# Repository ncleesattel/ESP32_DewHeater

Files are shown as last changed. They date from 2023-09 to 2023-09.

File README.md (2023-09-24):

# ESP32_DewHeater
Dew heater using the MyDewHeater from Robert Brown as starting point to understand circutry and software.

## Hardware Features
* Integration in Bopla Alubos case equal in size to the TeenAstro Main Unit.
* Design comprised of 3x pcbs
   * main dew heater circutry
   * connection panel top
   * sensor panel bottom
* Design uses SMDs to make use of the JLCPCB assembly service.

### Power Distribution
* Breakout DC-power jacks for
   * TeenAstro Main Unit
   * Intel NUC or Lenovo ThinkCentre
   * AstroCam
   * Filter-Rotator
### Dew Heater
* 3-Channel output that can be used for dew straps or a flat-field light.
* Use of high efficiency MOSFETs to eliminate need for heat sink.
* Integration of current and voltage sensors to calculate actual power output.
* Use of BME280 sensor to calculate dew point.
* Use of rotary pulse encoders to adjust power output.

## Software Features
* Bare knuckle software without closed-loop shenanigans.
* Read sensors and rotary pulse encoders.
* Calculate power output and dew point.
* Adjust output with enoder input only.

## BOM
What do you need for this build.
* dew_control_pcb
* dew_connector_pcb
* dew_sensor_pcb
* OLED 2.42" from DIYMORE configured to I2C or similar
* ESP32 30-pin MCU
* Bopla Alubos ABPH-1300-0150 bottom half
* 3D print for top cover which also fits display
* 3D print of side cover connector
* 3D print of side cover sensor
* 2x Mentor aluminum knobs 521.611
* 3x RCA connector Cliff FC68375
* 8x DC-jack Cliff FC681445 (5.5mm x 2.1mm type)
* 6x JST VH VHR-2N connectors for 3 cables
* 3x JST VH B2P-VH (LF) connector to solder to pcbs
* TE Mate N Lok 350211-1 connector to solder to pcb
* Marquart Series 1800 switch (on/off)
* Ruthex M2.5 threaded inserts

## Cost estimate
| Item | Number | Cost |
|-----|-----|-----|
| dew_control_pcb | 5 | 160|
| dew_sensor_pcb | 5 | 15|
| dew_connector_pcb | 5 | 15|
| ESP32 30-in MCU | 1 | 10|
| OLED 2.42 | 1 | 20|
| BOPLA Alubos ABPH 1300-0150 | 1 | 50|
| Cliff RCA connectors | 3 | 10 |
| Cliff DC jacks | 8 | 24 |
| various other | x | 20 |

Best case 170 Eur if you can share all pcbs  
Worst case 320 Eur if you keep all pcbs and build only one

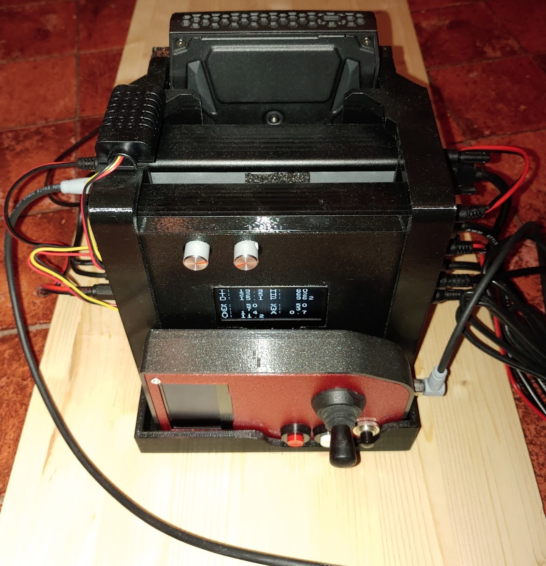
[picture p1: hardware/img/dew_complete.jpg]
running


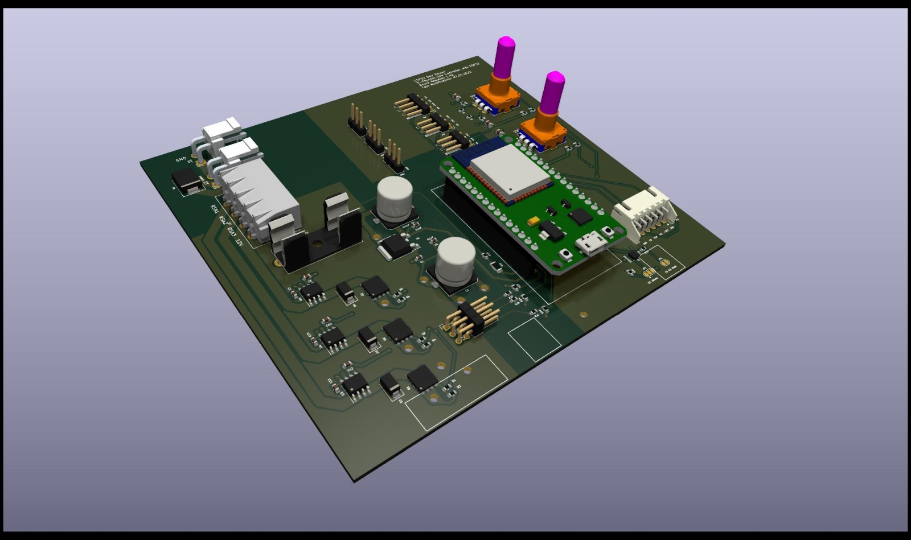
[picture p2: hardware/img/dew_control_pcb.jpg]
control_pcb


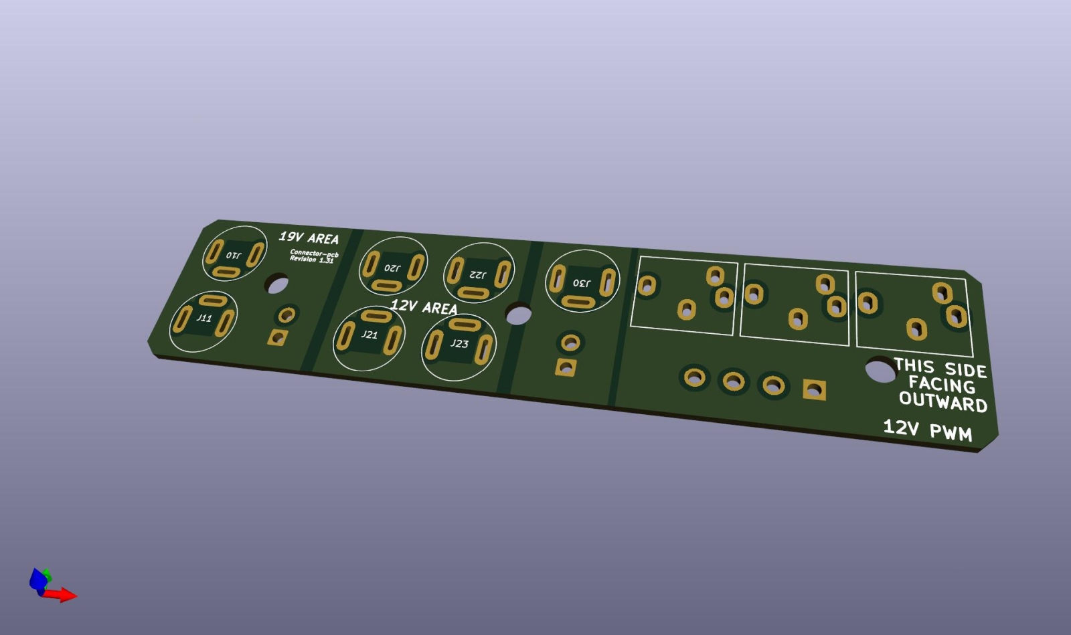
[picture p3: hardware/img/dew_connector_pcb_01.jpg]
connector_pcb


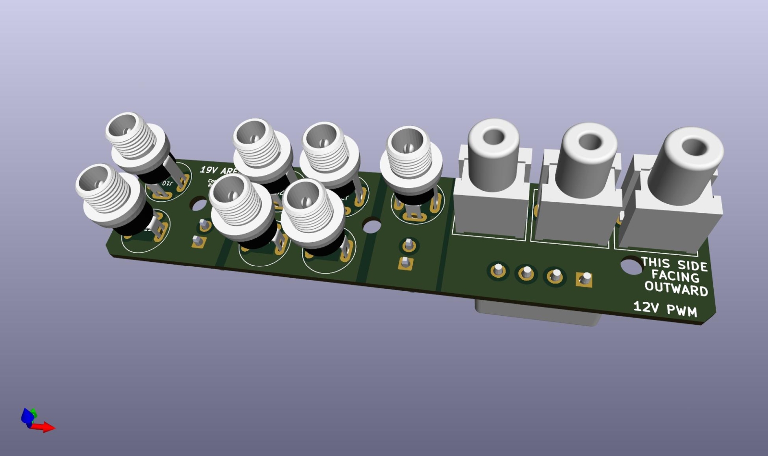
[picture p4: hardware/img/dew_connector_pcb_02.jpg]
connector_pcb


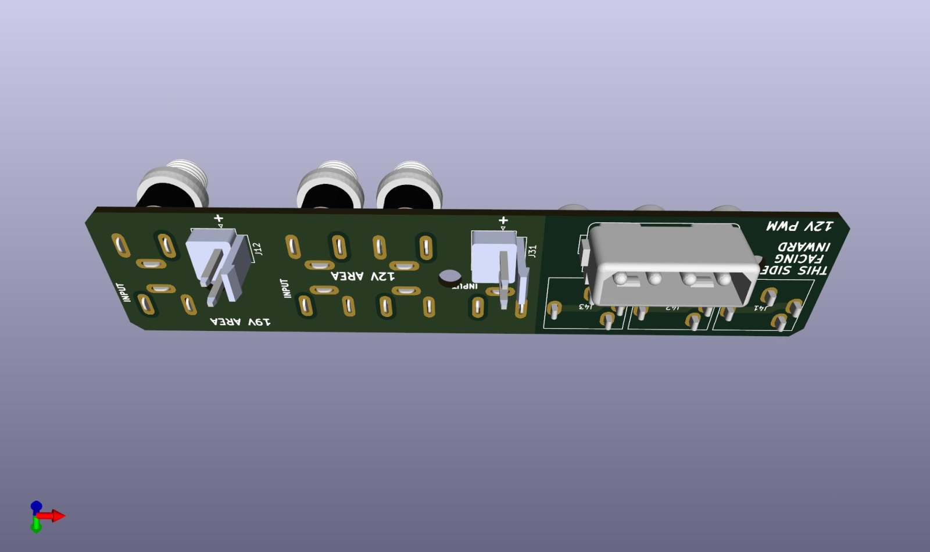
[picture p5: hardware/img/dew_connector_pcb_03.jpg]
connector_pcb


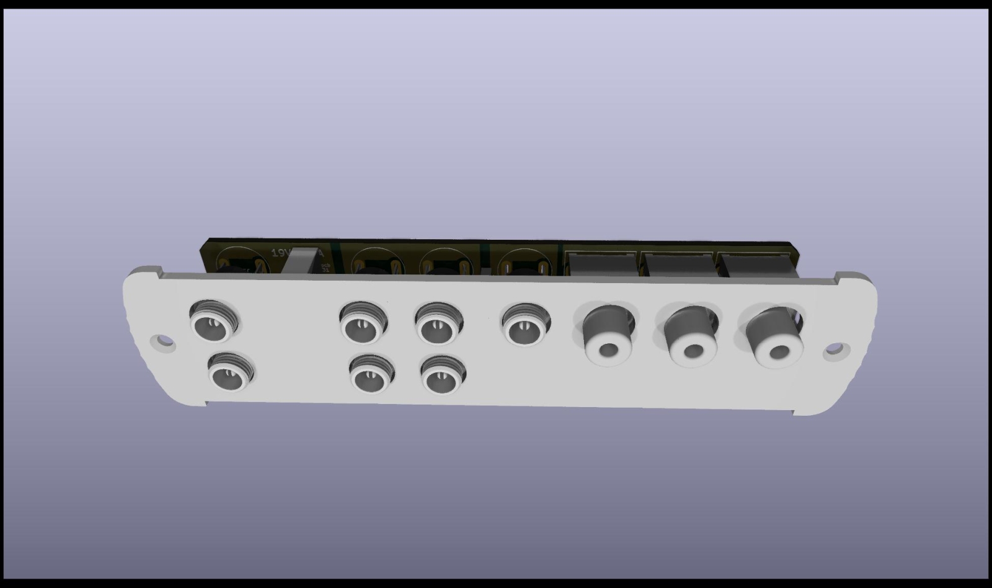
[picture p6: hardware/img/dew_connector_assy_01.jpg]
connector_assy


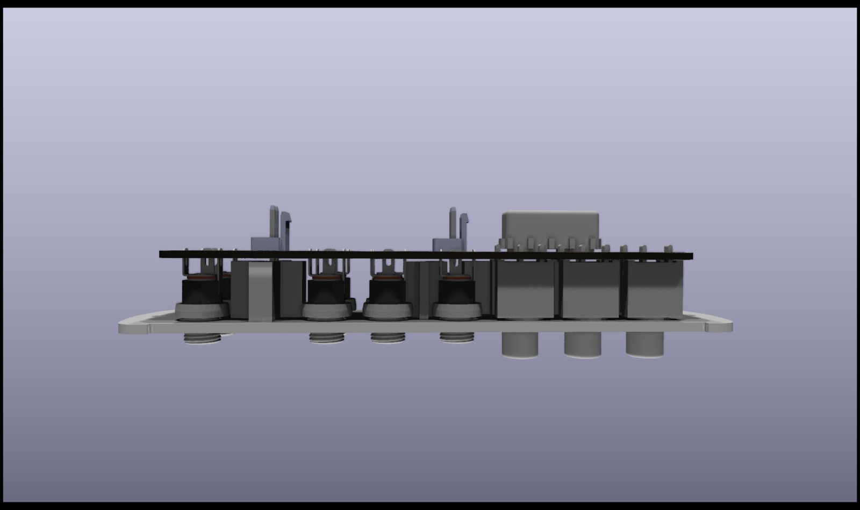
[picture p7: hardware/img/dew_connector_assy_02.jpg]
connector_assy


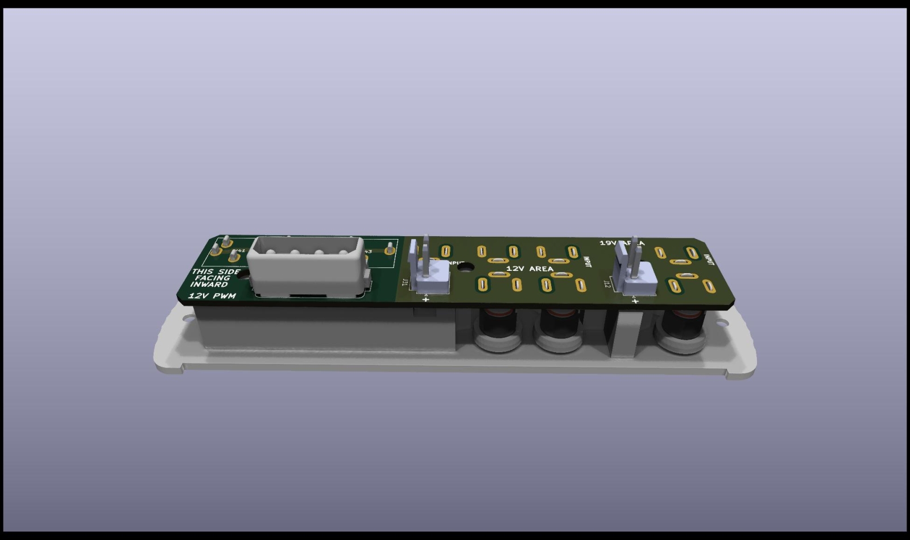
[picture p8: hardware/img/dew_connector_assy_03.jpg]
connector_assy


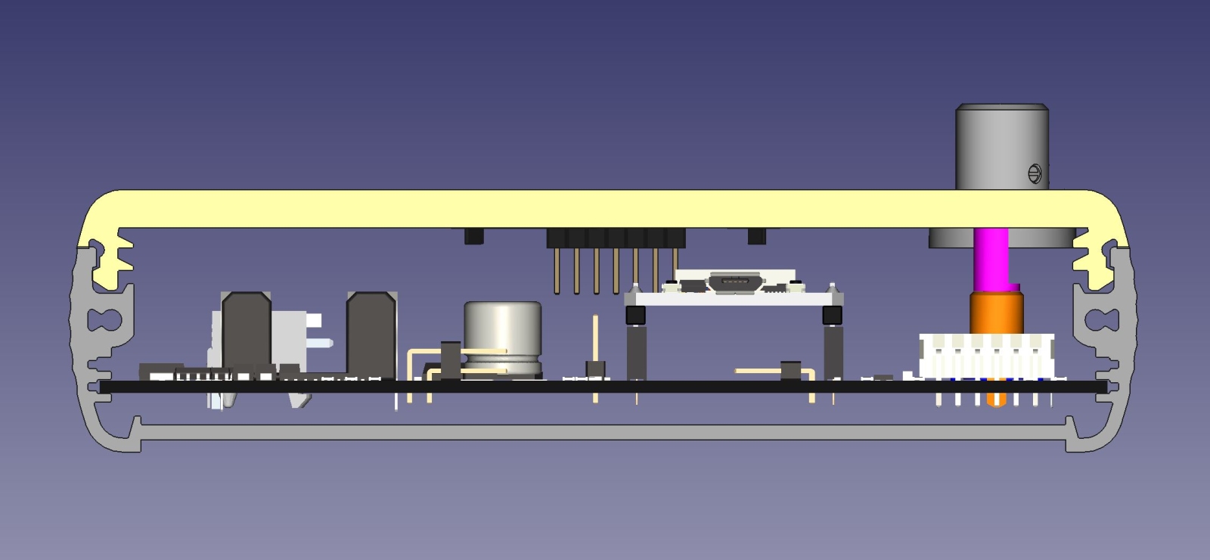
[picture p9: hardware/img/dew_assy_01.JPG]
dew_assy


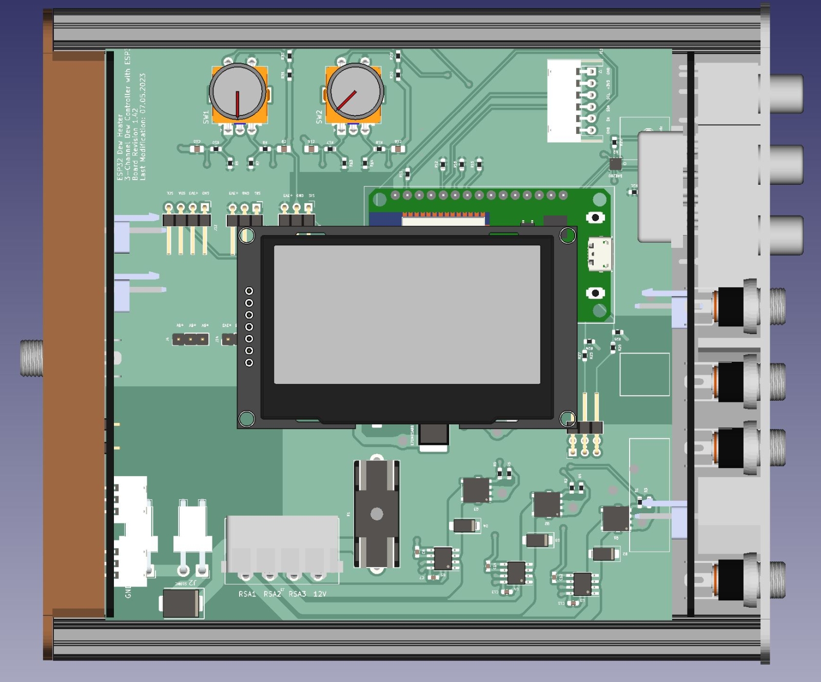
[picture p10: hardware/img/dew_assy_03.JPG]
dew_assy


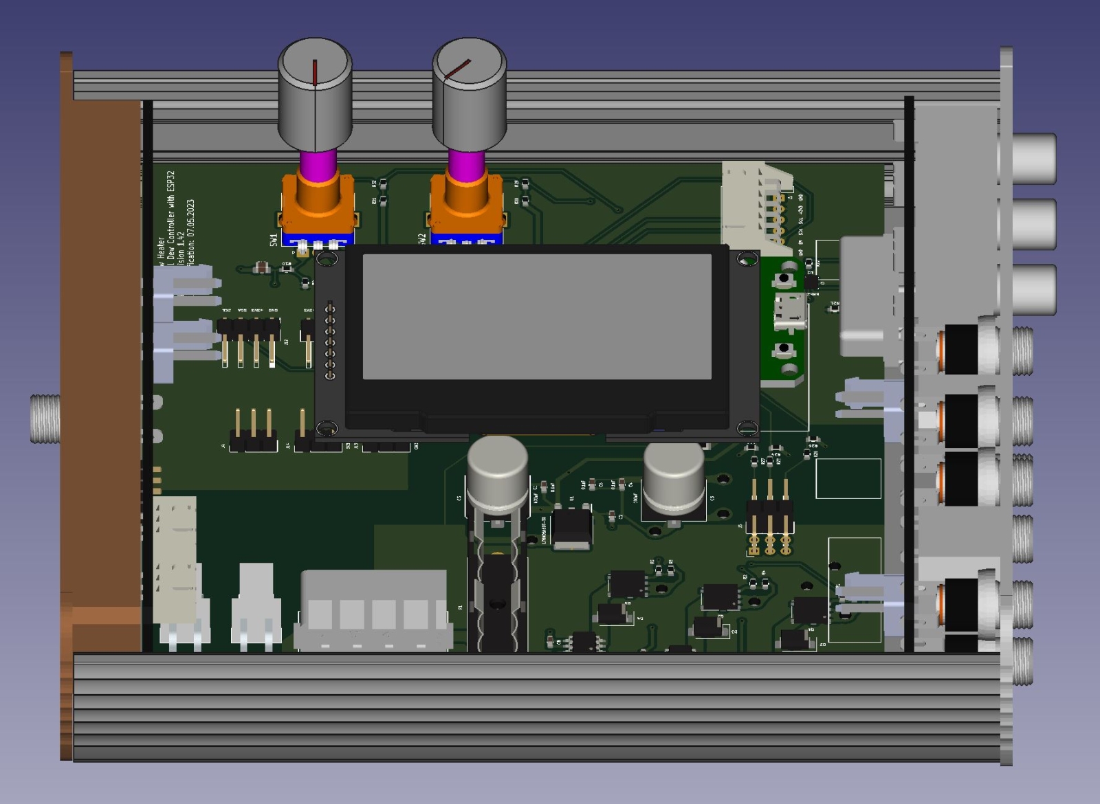
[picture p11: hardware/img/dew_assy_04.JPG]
dew_assy


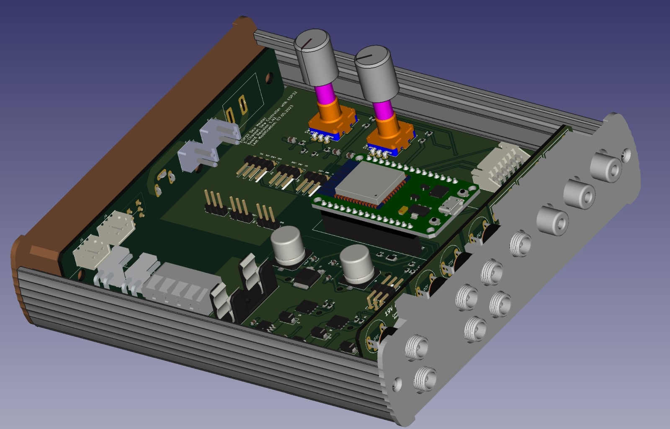
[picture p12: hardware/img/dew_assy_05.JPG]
dew_assy


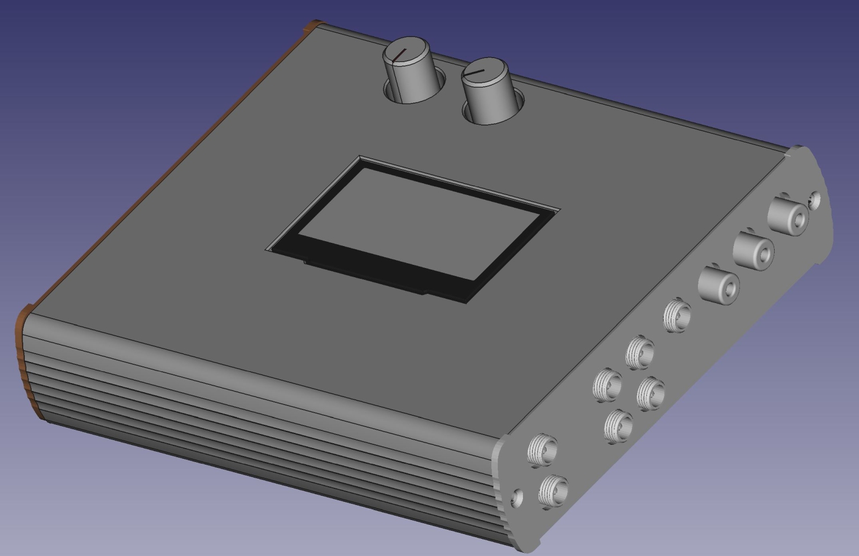
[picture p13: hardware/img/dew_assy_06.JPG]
dew_assy


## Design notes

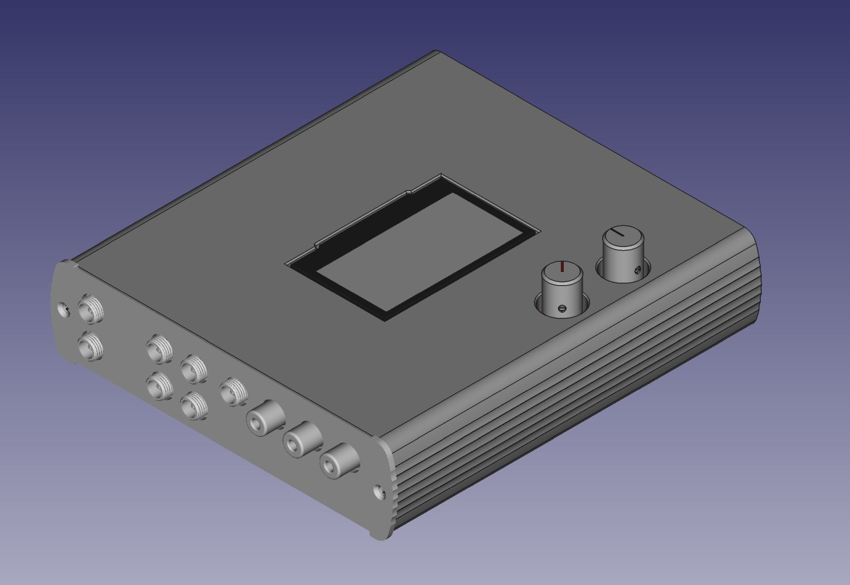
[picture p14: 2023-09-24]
hardware/img/dew_assy_02.JPG

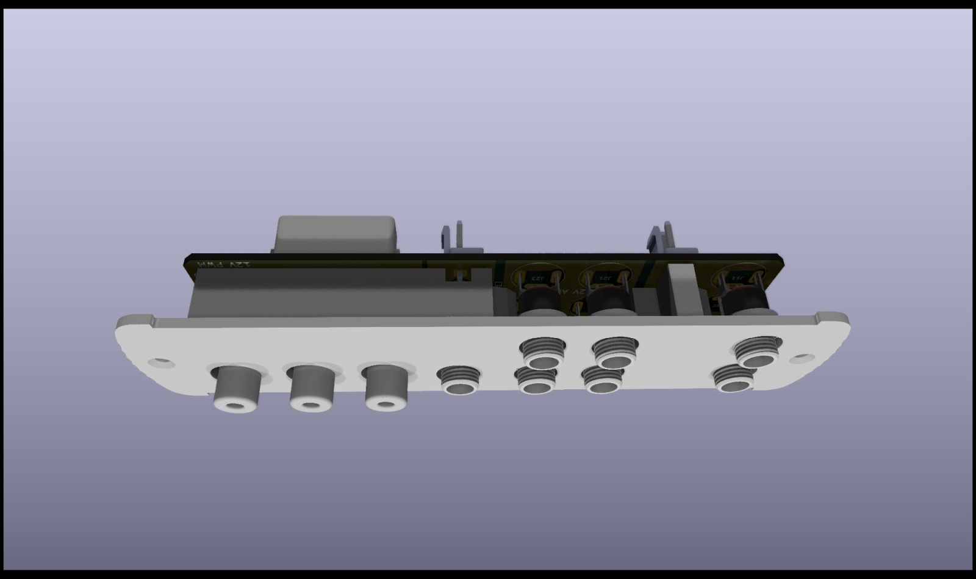
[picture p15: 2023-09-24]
hardware/img/dew_connector_assy_04.jpg

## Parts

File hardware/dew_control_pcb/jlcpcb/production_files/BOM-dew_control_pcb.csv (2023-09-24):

Comment | Designator | Footprint | LCSC
0.1uF | C1,C11,C13,C4,C6,C7 | C_0603_1608Metric | C14663
OLED | J11 | JST_XH_S6B-XH-A_1x06_P2.50mm_Horizontal | C157919
POWER | J1,J2 | JST_VH_S2P-VH_1x02_P3.96mm_Horizontal | C160355
0.33uF | C2 | C_0603_1608Metric | C1615
S10MC | D1 | D_SMC | C169472
NTMFS5C670NLT1G | Q1,Q2,Q3 | ONSemi_SO-8FL_488AA | C179626
Fuse | F1 | Fuseholder_Cylinder-5x20mm | C206887
150 | R1,R2,R5 | R_0603_1608Metric | C22808
15K | R23,R25,R27 | R_0603_1608Metric | C22809
4K7 | R11,R12,R15,R16,R20,R21 | R_0603_1608Metric | C23162
43k | R24,R26,R28 | R_0603_1608Metric | C23172
CURRENT EN | J5 | PinHeader_2x03_P2.54mm_Horizontal | C239334
10K | R10,R13,R14,R17,R18,R19,R29,R3,R30,R31,R32,R4,R6,R7,R8,R9 | R_0603_1608Metric | C25804
1.5K | R22 | R_1206_3216Metric | C26036
100uF | C5 | C_Elec_10x10.2 | C280414
I2C | J12 | PinHeader_1x04_P2.54mm_Horizontal | C293357
0.01uF | C10,C15,C16,C9 | C_0805_2012Metric | C376921
ACS712xLCTR-05B | U3,U4,U5 | SOIC-8_3.9x4.9mm_P1.27mm | C44471
RotaryEncoder_Switch | SW1,SW2 | RotaryEncoder_Alps_EC11E-Switch_Vertical_H20mm | C470754
RSA DEW | J3 | TE_MATE-N-LOK_1x04_P5.08mm_Horizontal | C492552
L78M05ABDT-TR | U1 | TO-252-2 | C58069
PROBE1 | J31,J32 | PinHeader_1x03_P2.54mm_Horizontal | C706866
470uF | C3 | C_Elec_10x10.2 | C72518
D_Schottky | D2,D3,D4 | D_SMA | C8678
1nF | C12,C14,C8 | C_0603_1608Metric | C8808
BME280 | U2 | Bosch_LGA-8_2.5x2.5mm_P0.65mm_ClockwisePinNumbering | C92489
I2C Adress | JP2 | SolderJumper-3_P1.3mm_Bridged12_RoundedPad1.0x1.5mm
3V3 | J14 | PinHeader_1x03_P2.54mm_Vertical
GND | J13 | PinHeader_1x03_P2.54mm_Vertical
ESP32-30pin | IC1 | ESP32-30pin
5V | J4 | PinHeader_1x03_P2.54mm_Vertical
EN I2C Mode | JP1 | SolderJumper-2_P1.3mm_Bridged_RoundedPad1.0x1.5mm

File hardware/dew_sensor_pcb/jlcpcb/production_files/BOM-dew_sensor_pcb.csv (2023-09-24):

Comment | Designator | Footprint | LCSC
Conn_01x03 | J7 | PinHeader_1x03_P2.54mm_Vertical
Conn_01x02 | J1 | JST_VH_B2P-VH-B_1x02_P3.96mm_Vertical
Conn_01x02 | J2 | JST_VH_B2P-VH-B_1x02_P3.96mm_Vertical
SW_SPST | SW1 | Marquart
Conn_01x03 | J4 | JST_XH_B3B-XH-A_1x03_P2.50mm_Vertical
Conn_01x03 | J6 | JST_XH_B3B-XH-A_1x03_P2.50mm_Vertical
Conn_01x03 | J5 | PinHeader_1x03_P2.54mm_Vertical
Barrel_Jack_MountingPin | J8 | BarrelJack_Vertical

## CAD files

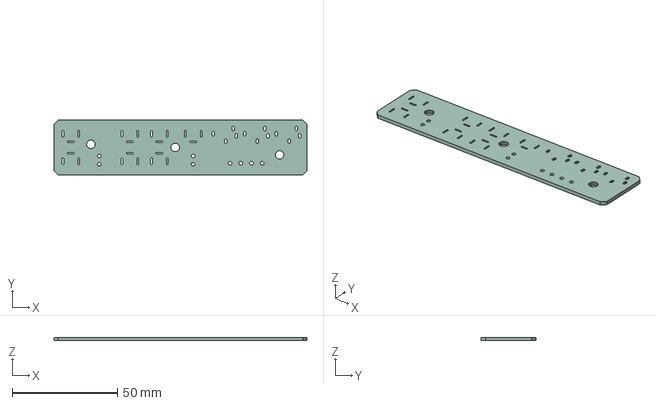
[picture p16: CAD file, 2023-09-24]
hardware/dew_connector_pcb/dew_connector_pcb.step
120.0 x 26.0 x 1.58 mm

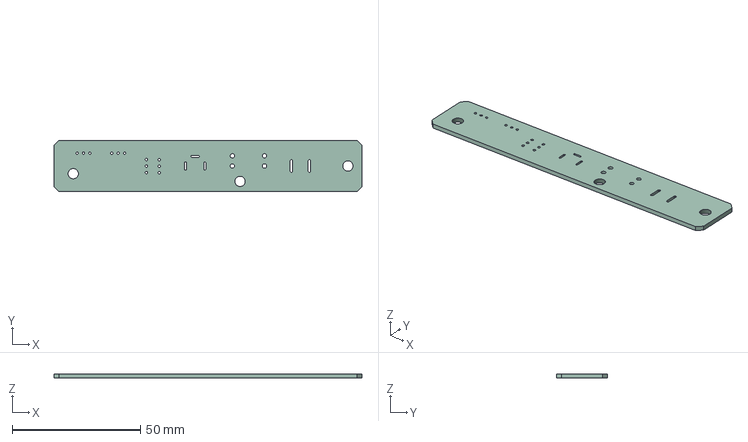
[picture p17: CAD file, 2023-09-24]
hardware/dew_sensor_pcb/dew_sensor_pcb.step
120.0 x 20.0 x 1.58 mm

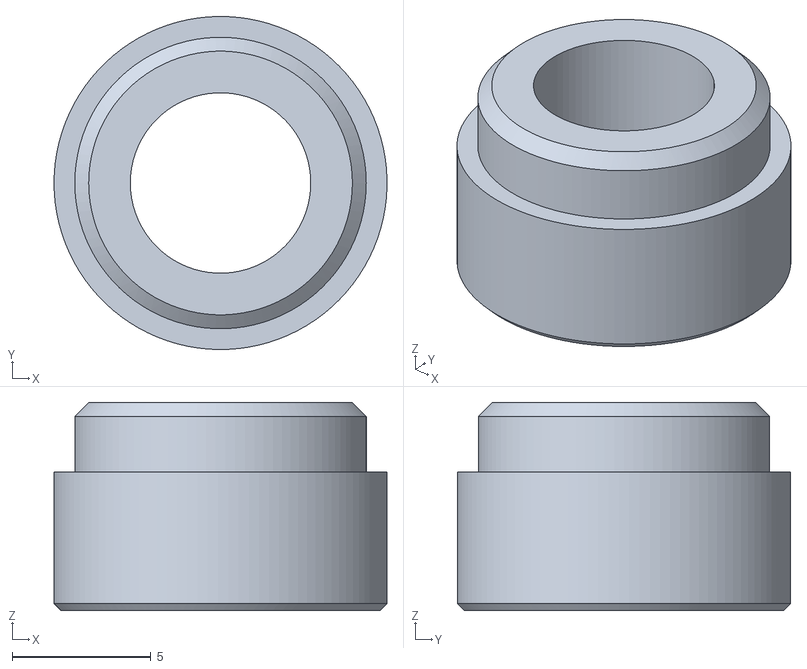
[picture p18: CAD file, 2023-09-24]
hardware/models/KNOB_SOCKET.stl
12.0 x 12.0 x 7.50

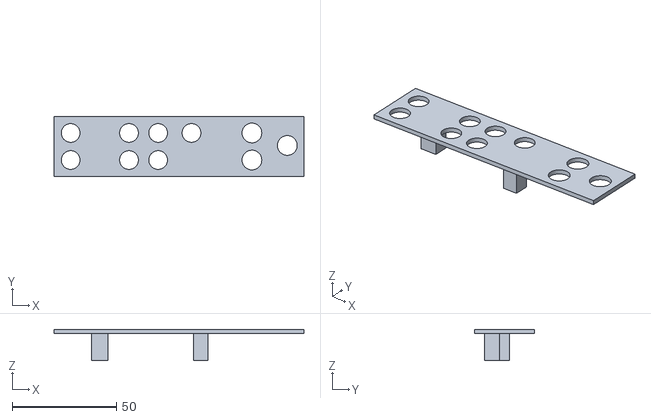
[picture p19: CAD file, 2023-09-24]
hardware/models/SOLDERING_HELP.stl
120.0 x 29.0 x 15.0

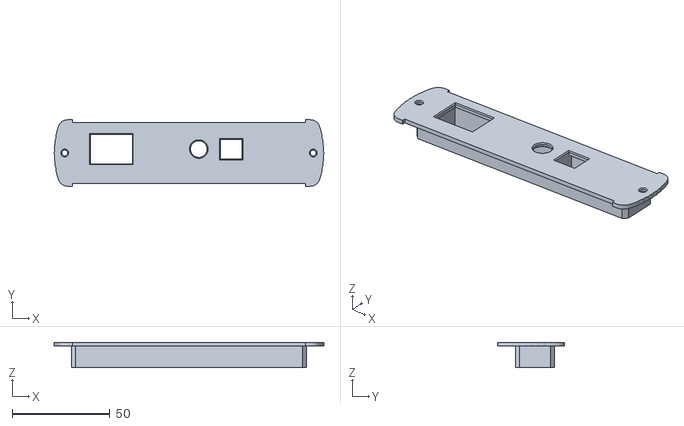
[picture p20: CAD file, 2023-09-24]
hardware/models/OUTPUT_PRINT.stl
138.0 x 34.0 x 13.0

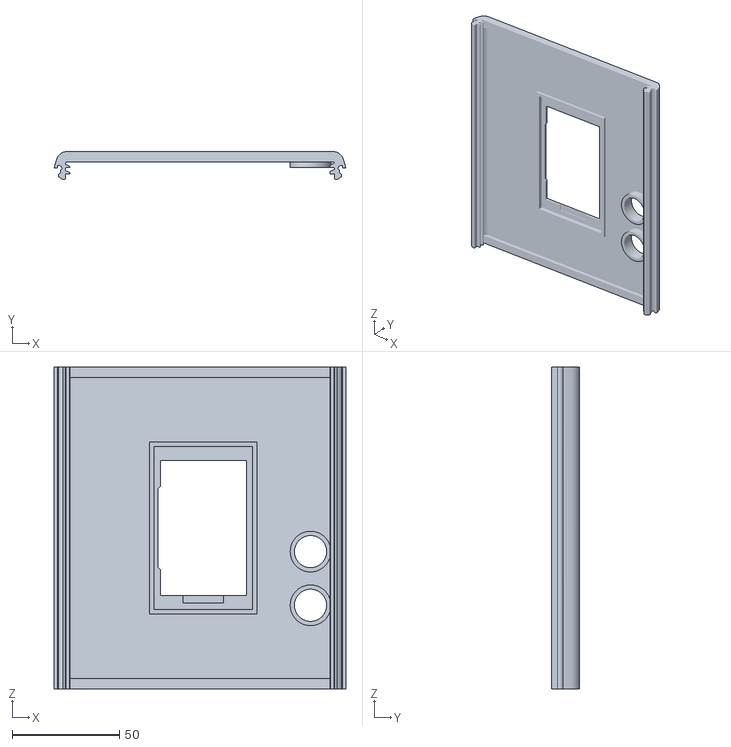
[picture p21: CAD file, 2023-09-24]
hardware/models/DISPLAY_PRINT.stl
135.8 x 13.0 x 150.0

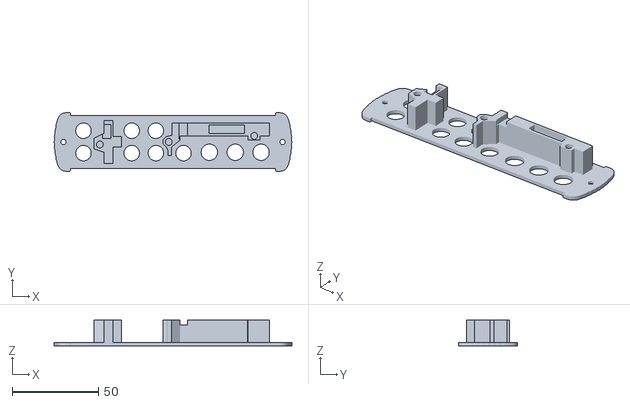
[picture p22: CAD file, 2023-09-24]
hardware/models/CONNECTOR_PRINT.stl
138.0 x 34.0 x 15.0

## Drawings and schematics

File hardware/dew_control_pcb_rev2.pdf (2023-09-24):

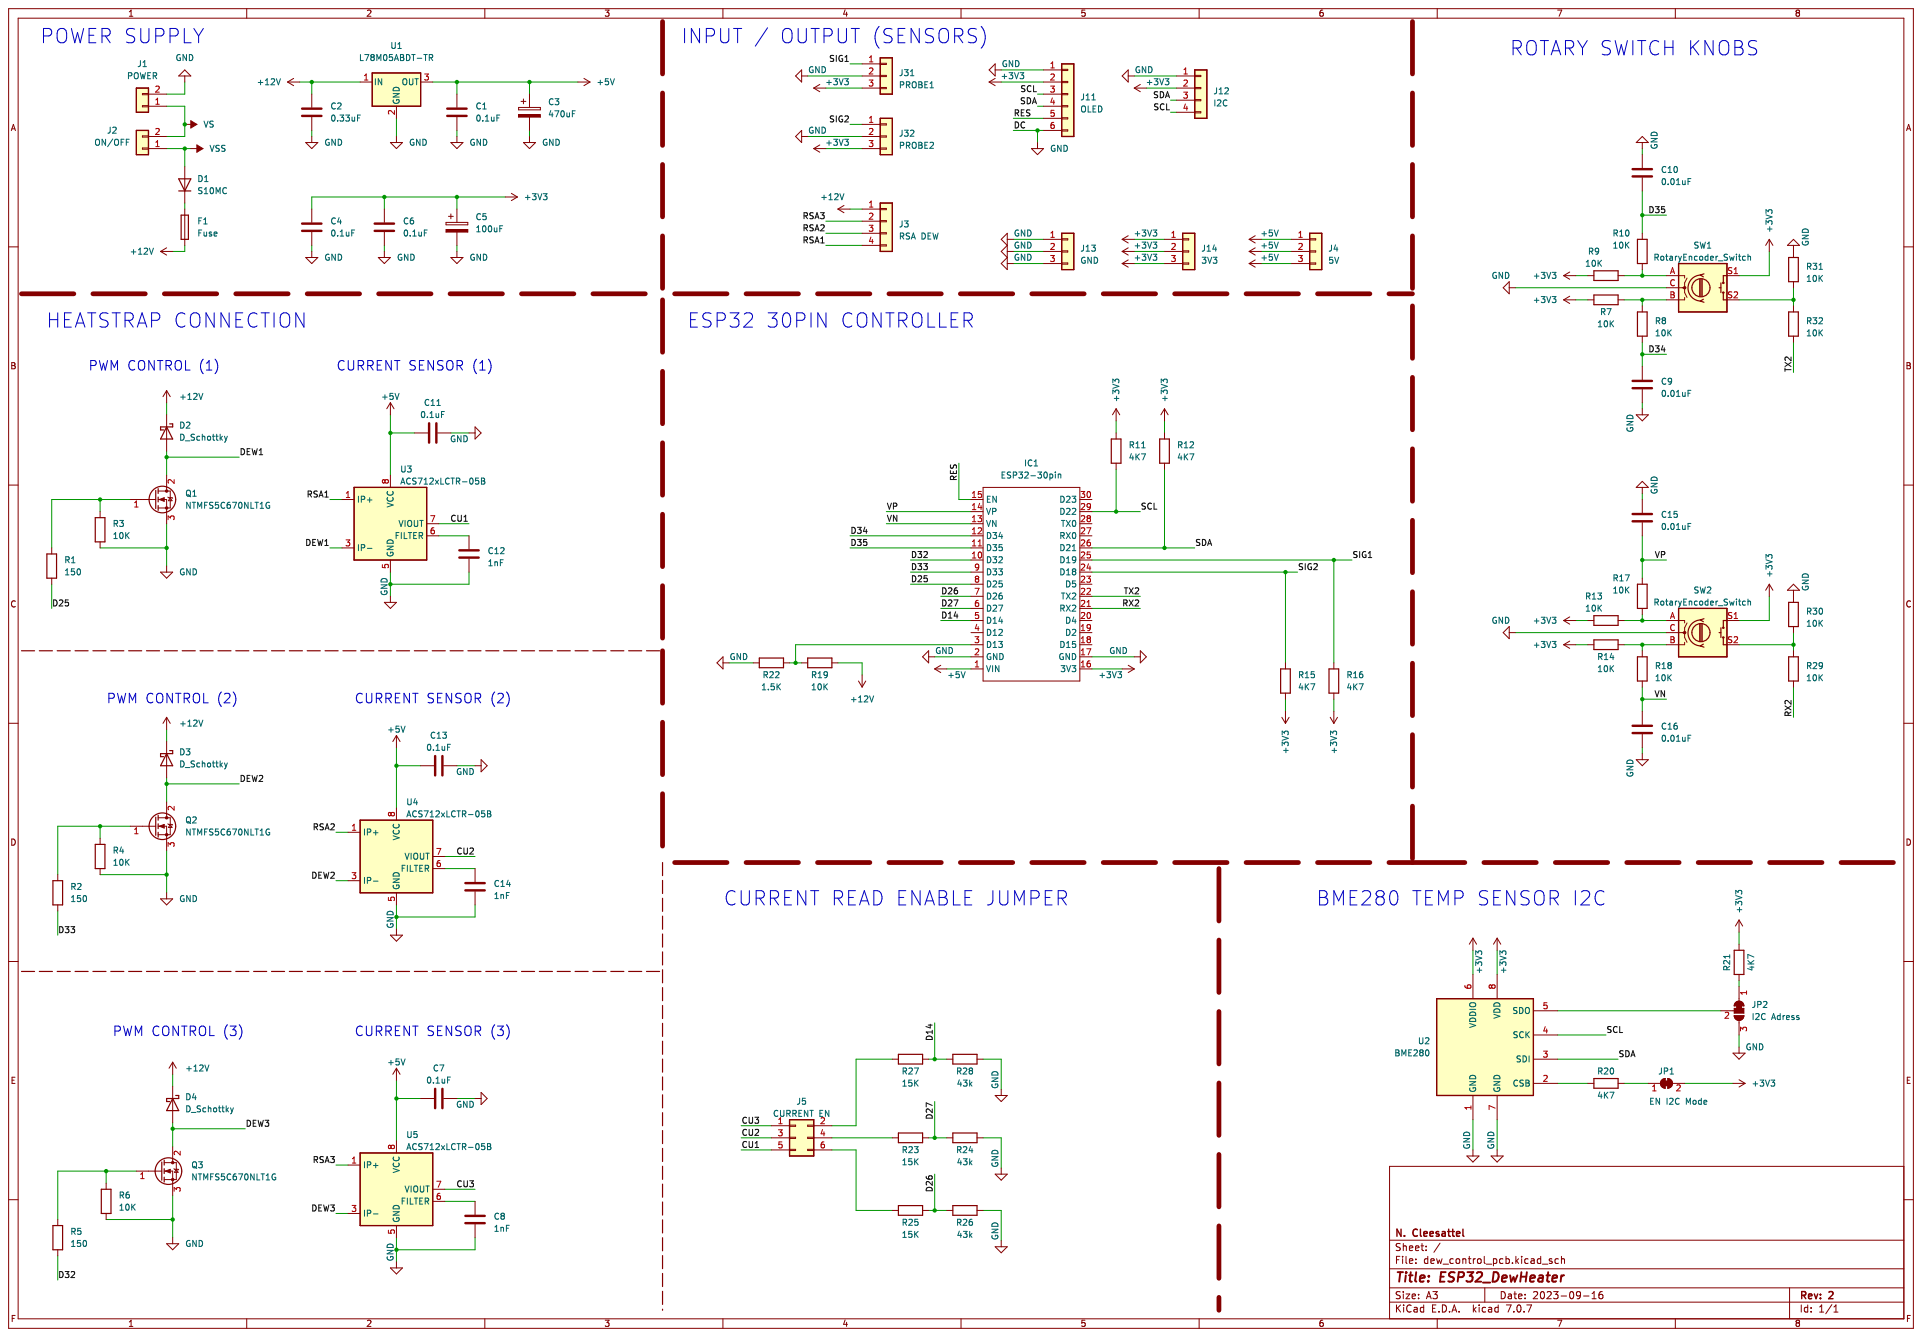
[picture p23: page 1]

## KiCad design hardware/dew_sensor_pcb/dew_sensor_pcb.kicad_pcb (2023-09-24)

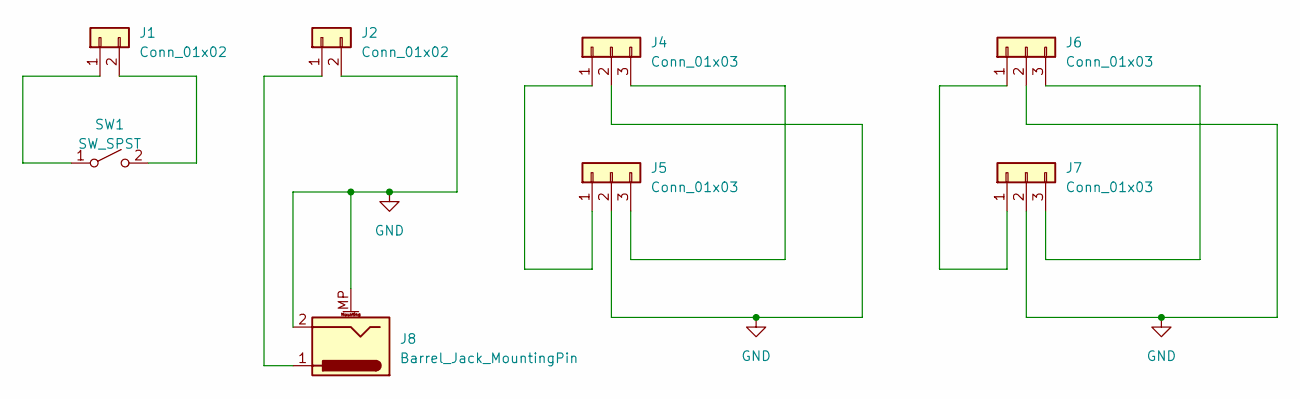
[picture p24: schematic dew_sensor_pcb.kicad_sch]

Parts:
J1, J2: Conn_01x02; JST_VH_B2P-VH-B_1x02_P3.96mm_Vertical
J4, J6: Conn_01x03; JST_XH_B3B-XH-A_1x03_P2.50mm_Vertical
J5, J7: Conn_01x03; PinHeader_1x03_P2.54mm_Vertical
J8: Barrel_Jack_MountingPin; BarrelJack_Vertical
SW1: SW_SPST; Marquart

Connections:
GND: J2.2, J4.2, J5.2, J6.2, J7.2, J8.2, J8.MP (MountPin)
unnamed: J1.1, SW1.1 (A)
unnamed: J1.2, SW1.2 (B)
unnamed: J2.1, J8.1
unnamed: J4.1, J5.1
unnamed: J4.3, J5.3
unnamed: J6.1, J7.1
unnamed: J6.3, J7.3

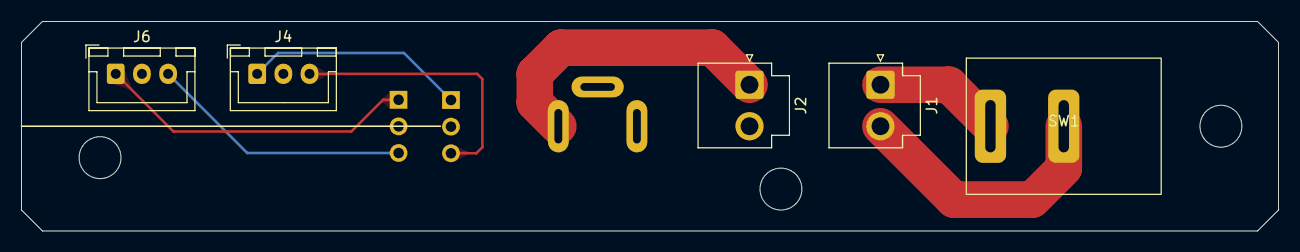
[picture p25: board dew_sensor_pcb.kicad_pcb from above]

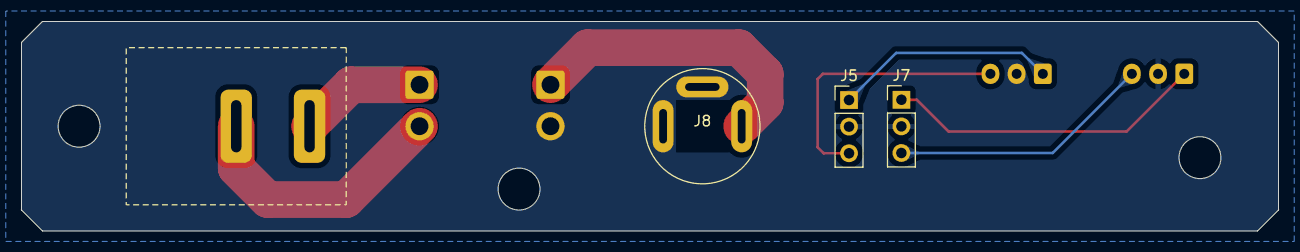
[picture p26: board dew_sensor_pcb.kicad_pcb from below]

Board: 2 copper layers, 120.0 x 20.0 mm, 8 parts (3 on the bottom side), 8 nets.

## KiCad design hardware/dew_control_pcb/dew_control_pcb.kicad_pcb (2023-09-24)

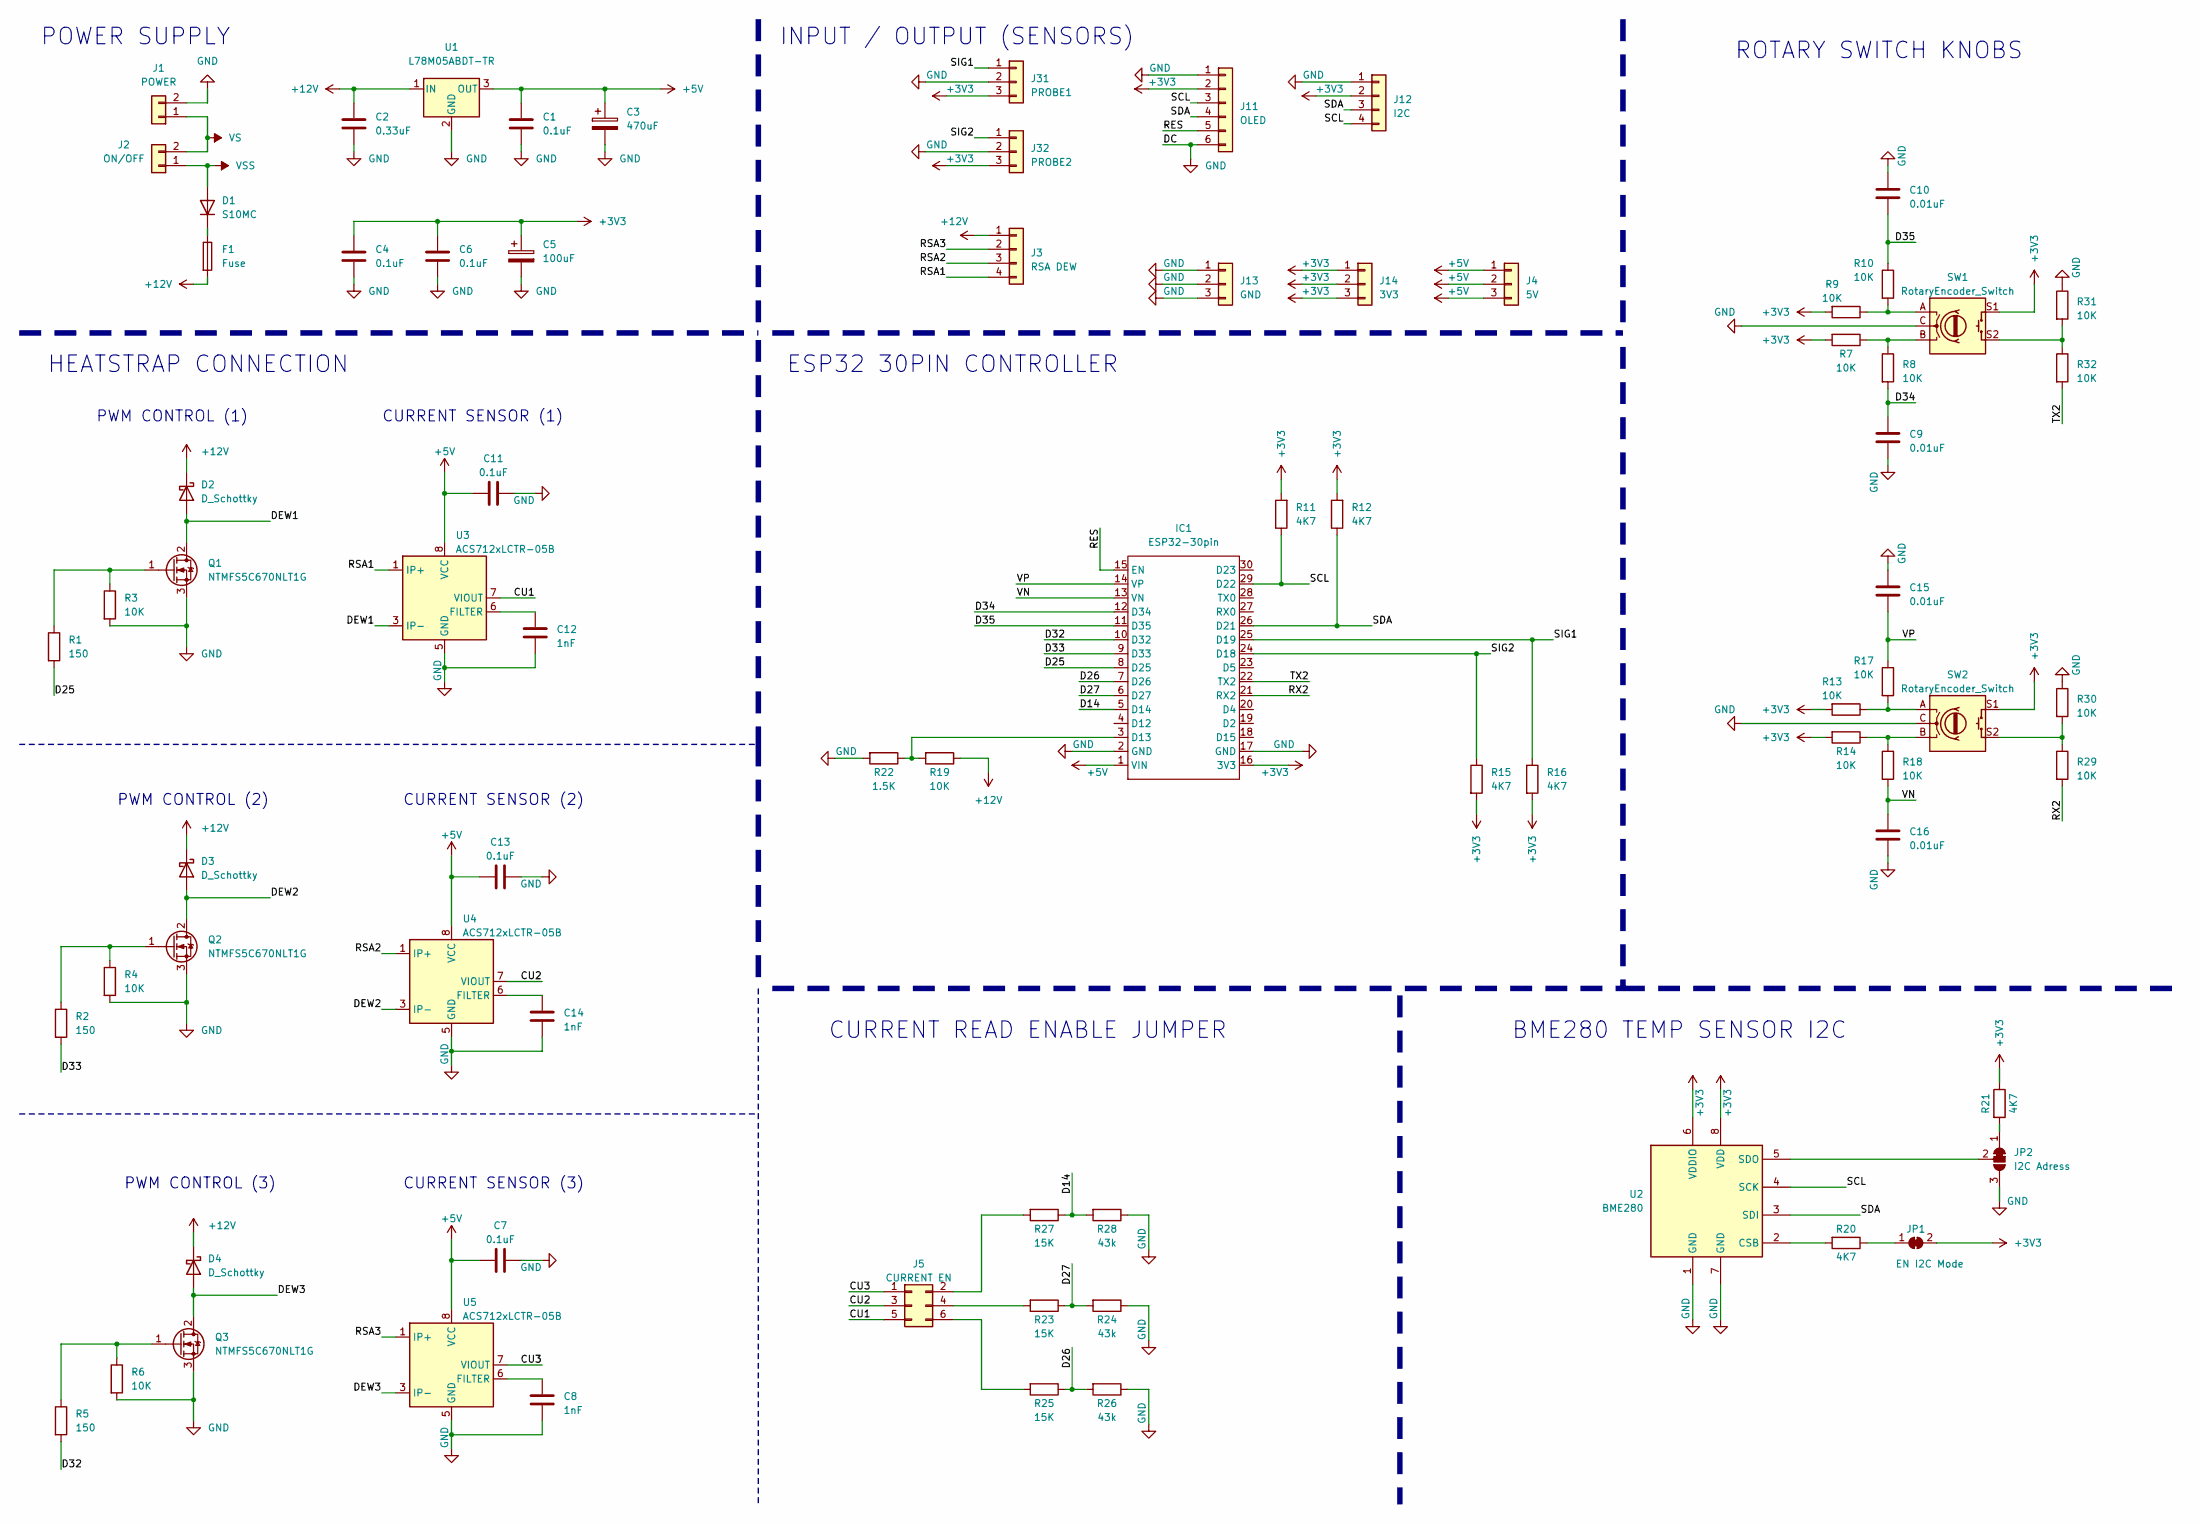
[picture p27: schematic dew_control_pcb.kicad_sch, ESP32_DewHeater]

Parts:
C1, C4, C6, C7, C11, C13: 0.1uF; C_0603_1608Metric; LCSC C14663
C2: 0.33uF; C_0603_1608Metric; LCSC C1615
C3: 470uF; C_Elec_10x10.2; LCSC C72518
C5: 100uF; C_Elec_10x10.2; LCSC C280414
C8, C12, C14: 1nF; C_0603_1608Metric; LCSC C8808
C9, C10, C15, C16: 0.01uF; C_0805_2012Metric; LCSC C376921
D1: S10MC; D_SMC; LCSC C169472
D2, D3, D4: D_Schottky; D_SMA; JLCPCB C8678
F1: Fuse; Fuseholder_Cylinder-5x20mm; LCSC C206887
IC1: ESP32-30pin
J1: POWER; JST_VH_S2P-VH_1x02_P3.96mm_Horizontal; LCSC C160355
J2: ON/OFF; JST_VH_S2P-VH_1x02_P3.96mm_Horizontal; LCSC C160355
J3: RSA DEW; TE_MATE-N-LOK_1x04_P5.08mm_Horizontal; LCSC C492552
J4: 5V; PinHeader_1x03_P2.54mm_Vertical
J5: CURRENT EN; PinHeader_2x03_P2.54mm_Horizontal; LCSC C239334
J11: OLED; JST_XH_S6B-XH-A_1x06_P2.50mm_Horizontal; LCSC C157919
J12: I2C; PinHeader_1x04_P2.54mm_Horizontal; LCSC C293357
J13: GND; PinHeader_1x03_P2.54mm_Vertical
J14: 3V3; PinHeader_1x03_P2.54mm_Vertical
J31: PROBE1; PinHeader_1x03_P2.54mm_Horizontal; LCSC C706866
J32: PROBE2; PinHeader_1x03_P2.54mm_Horizontal; LCSC C706866
JP1: EN I2C Mode; SolderJumper-2_P1.3mm_Bridged_RoundedPad1.0x1.5mm
JP2: I2C Adress; SolderJumper-3_P1.3mm_Bridged12_RoundedPad1.0x1.5mm
Q1, Q2, Q3: NTMFS5C670NLT1G; ONSemi_SO-8FL_488AA; LCSC C179626
R1, R2, R5: 150; R_0603_1608Metric; LCSC C22808
R3, R4, R6, R7, R8, R9, R10, R13, R14, R17, R18, R19, R29, R30, R31, R32: 10K; R_0603_1608Metric; LCSC C25804
R11, R12, R15, R16, R20, R21: 4K7; R_0603_1608Metric; LCSC C23162
R22: 1.5K; R_1206_3216Metric; LCSC C26036
R23, R25, R27: 15K; R_0603_1608Metric; LCSC C22809
R24, R26, R28: 43k; R_0603_1608Metric; LCSC C23172
SW1, SW2: RotaryEncoder_Switch; RotaryEncoder_Alps_EC11E-Switch_Vertical_H20mm; LCSC C470754
U1: L78M05ABDT-TR; TO-252-2; LCSC C58069
U2: BME280; Bosch_LGA-8_2.5x2.5mm_P0.65mm_ClockwisePinNumbering; LCSC C92489
U3, U4, U5: ACS712xLCTR-05B; SOIC-8_3.9x4.9mm_P1.27mm; LCSC C44471

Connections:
+3V3: C4.1, C5.1, C6.1, IC1.16 (3V3), J11.2, J12.2, J14.1, J14.2, J14.3, J31.3, J32.3, JP1.2 (B), R7.2, R9.2, R11.2, R12.2, R13.2, R14.2, R15.2, R16.2, R21.1, SW1.S1, SW2.S1, U2.6 (VDDIO), U2.8 (VDD)
+5V: C1.1, C3.1, C7.1, C11.1, C13.1, IC1.1 (VIN), J4.1, J4.2, J4.3, U1.3 (OUT), U3.8 (VCC), U4.8 (VCC), U5.8 (VCC)
+12V: C2.1, D2.1 (K), D3.1 (K), D4.1 (K), F1.2, J3.1, R19.1, U1.1 (IN)
/CU1: J5.5, U3.7 (VIOUT)
/CU2: J5.3, U4.7 (VIOUT)
/CU3: J5.1, U5.7 (VIOUT)
/D14: IC1.5 (D14), R27.1, R28.2
/D25: IC1.8 (D25), R1.2
/D26: IC1.7 (D26), R25.1, R26.2
/D27: IC1.6 (D27), R23.1, R24.2
/D32: IC1.10 (D32), R5.2
/D33: IC1.9 (D33), R2.2
/D34: C9.1, IC1.12 (D34), R8.2
/D35: C10.2, IC1.11 (D35), R10.1
/DEW1: D2.2 (A), Q1.2 (D), U3.3 (IP-), U3.4 (IP-)
/DEW2: D3.2 (A), Q2.2 (D), U4.3 (IP-), U4.4 (IP-)
/DEW3: D4.2 (A), Q3.2 (D), U5.3 (IP-), U5.4 (IP-)
/RES: IC1.15 (EN), J11.5
/RSA1: J3.4, U3.1 (IP+), U3.2 (IP+)
/RSA2: J3.3, U4.1 (IP+), U4.2 (IP+)
/RSA3: J3.2, U5.1 (IP+), U5.2 (IP+)
/RX2: IC1.21 (RX2), R29.2
/SCL: IC1.29 (D22), J11.3, J12.4, R11.1, U2.4 (SCK)
/SDA: IC1.26 (D21), J11.4, J12.3, R12.1, U2.3 (SDI)
/SIG1: IC1.25 (D19), J31.1, R16.1
/SIG2: IC1.24 (D18), J32.1, R15.1
/TX2: IC1.22 (TX2), R32.2
/VN: C16.1, IC1.13 (VN), R18.2
/VP: C15.2, IC1.14 (VP), R17.1
GND: C1.2, C2.2, C3.2, C4.2, C5.2, C6.2, C7.2, C8.1, C9.2, C10.1, C11.2, C12.1, C13.2, C14.1, C15.1, C16.2, IC1.2 (GND), IC1.17 (GND), J1.2, J11.1, J11.6, J12.1, J13.1, J13.2, J13.3, J31.2, J32.2, JP2.3 (B), Q1.3 (S), Q2.3 (S), Q3.3 (S), R3.2, R4.2, R6.2, R22.2, R24.1, R26.1, R28.1, R30.1, R31.1, SW1.C, SW2.C, U1.2 (GND), U2.1 (GND), U2.7 (GND), U3.5 (GND), U4.5 (GND), U5.5 (GND)
unnamed: D1.1 (K), F1.1
unnamed: IC1.3 (D13), R19.2, R22.1
unnamed: J5.2, R27.2
unnamed: J5.4, R23.2
unnamed: J5.6, R25.2
unnamed: JP1.1 (A), R20.1
unnamed: JP2.1 (A), R21.2
unnamed: JP2.2 (C), U2.5 (SDO)
unnamed: Q1.1 (G), R1.1, R3.1
unnamed: Q2.1 (G), R2.1, R4.1
unnamed: Q3.1 (G), R5.1, R6.1
unnamed: R7.1, R8.1, SW1.B
unnamed: R9.1, R10.2, SW1.A
unnamed: R13.1, R17.2, SW2.A
unnamed: R14.1, R18.1, SW2.B
unnamed: R29.1, R30.2, SW2.S2
unnamed: R31.2, R32.1, SW1.S2
unnamed: R20.2, U2.2 (CSB)
unnamed: C12.2, U3.6 (FILTER)
unnamed: C14.2, U4.6 (FILTER)
unnamed: C8.2, U5.6 (FILTER)
VS: J1.1, J2.2
VSS: D1.2 (A), J2.1

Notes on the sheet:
PWM CONTROL (2)
INPUT / OUTPUT (SENSORS)
PWM CONTROL (1)
HEATSTRAP CONNECTION
ESP32 30PIN CONTROLLER
CURRENT SENSOR (1)
ROTARY SWITCH KNOBS
BME280 TEMP SENSOR I2C
CURRENT SENSOR (2)
CURRENT SENSOR (3)
PWM CONTROL (3)
CURRENT READ ENABLE JUMPER
POWER SUPPLY

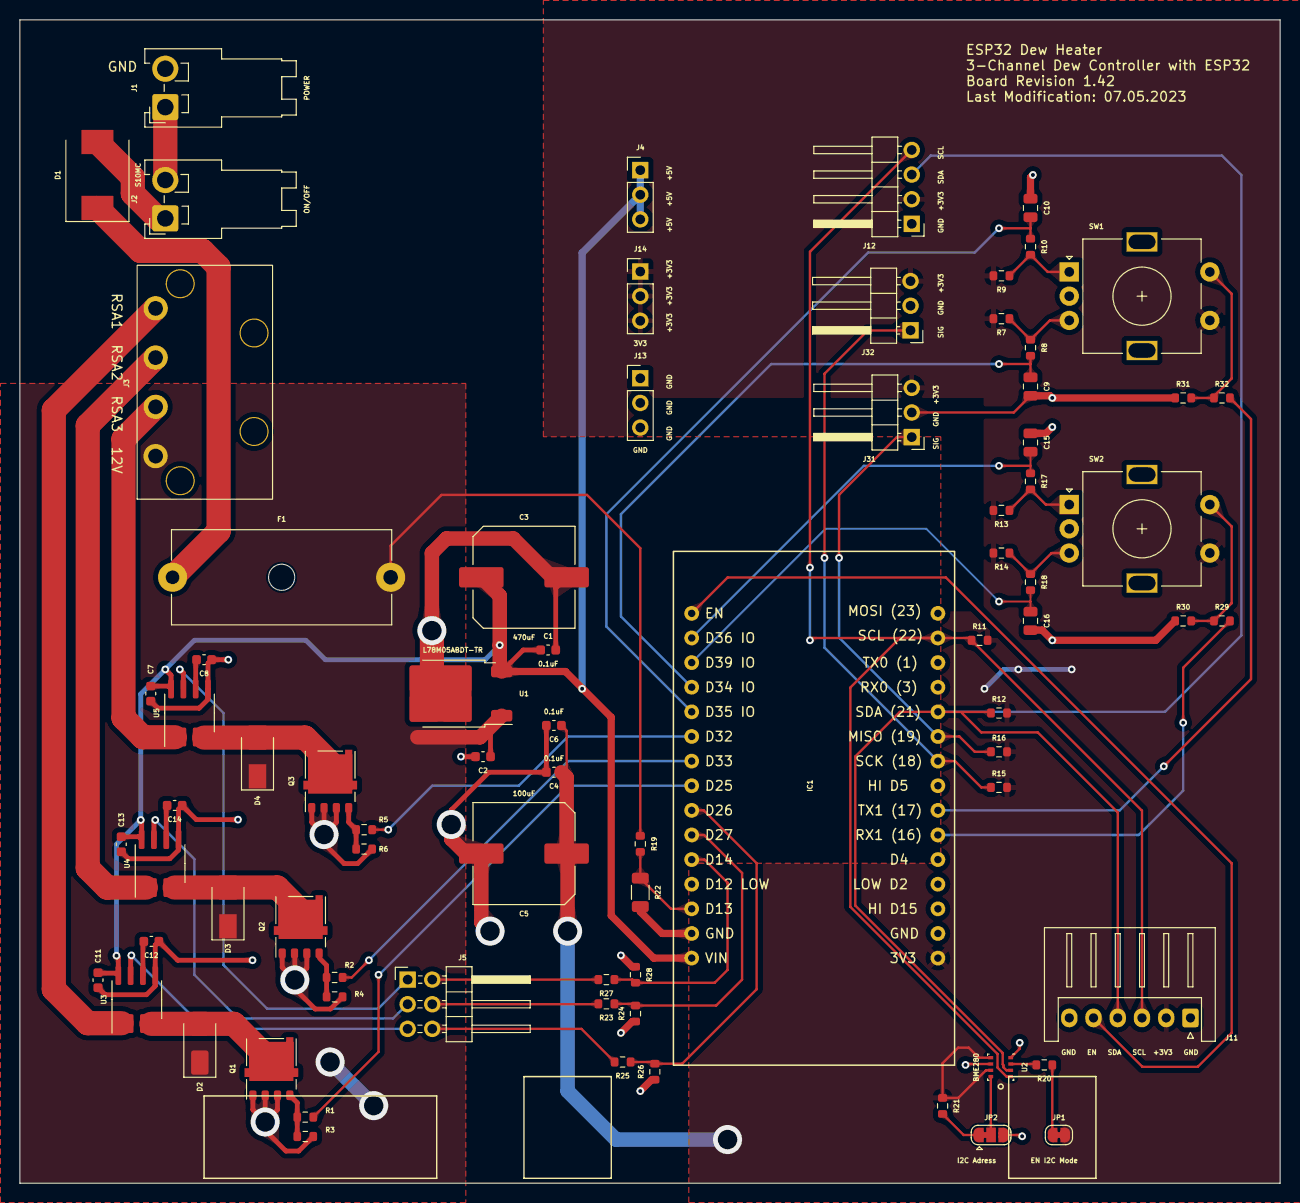
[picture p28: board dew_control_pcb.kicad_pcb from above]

Board: 2 copper layers, 130.0 x 120.0 mm, 77 parts (0 on the bottom side), 53 nets.

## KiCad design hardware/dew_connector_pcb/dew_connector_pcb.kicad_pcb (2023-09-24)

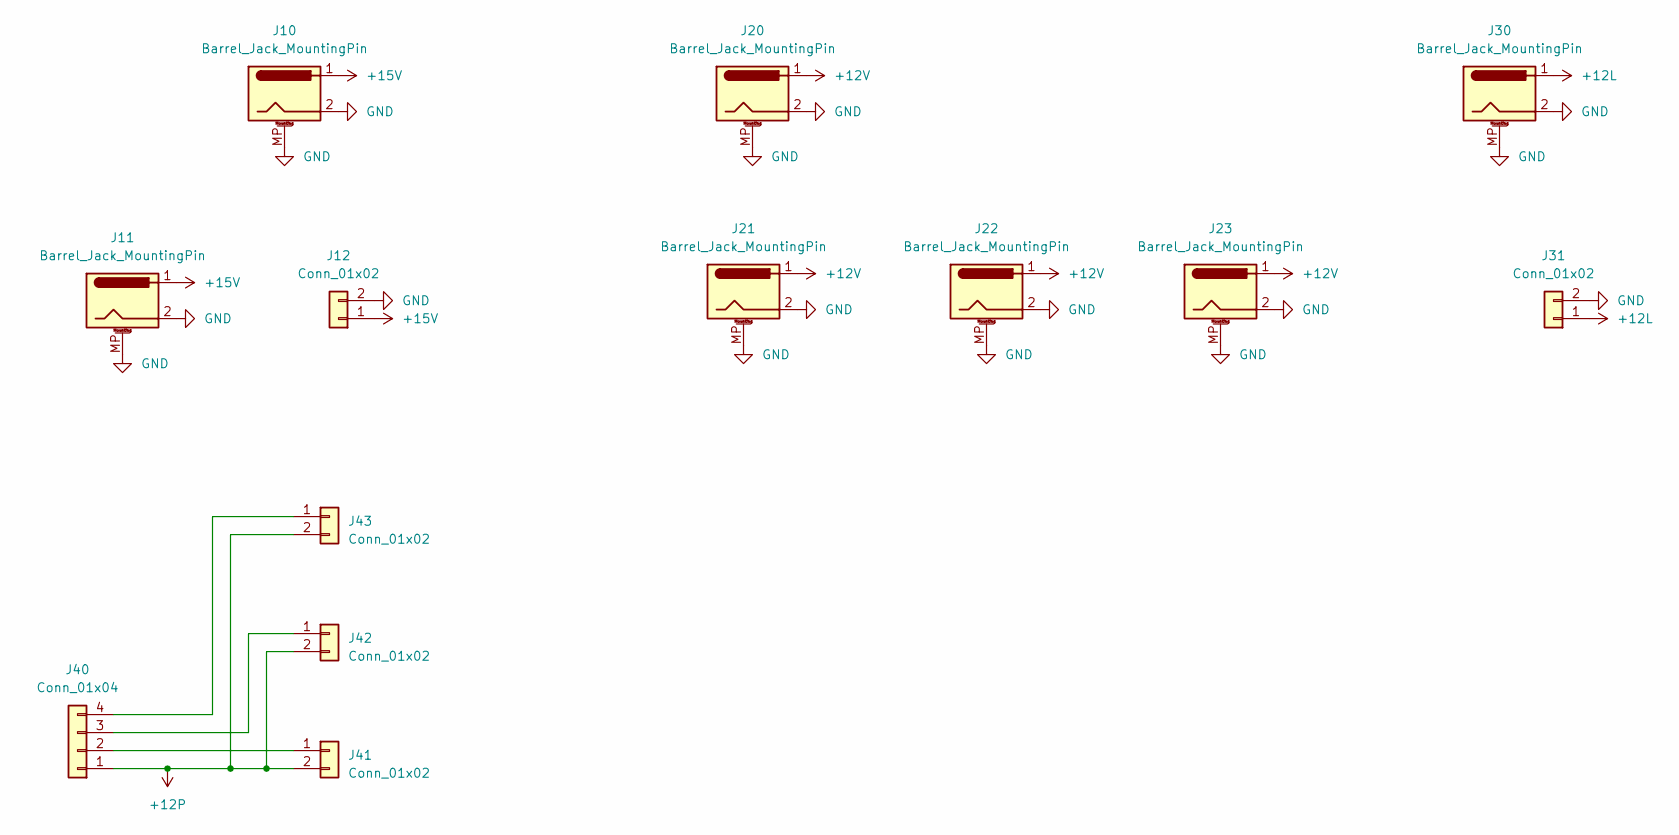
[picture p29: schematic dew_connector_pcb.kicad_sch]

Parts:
J10, J11, J20, J21, J22, J23, J30: Barrel_Jack_MountingPin; BarrelJack_Vertical
J12, J31: Conn_01x02; JST_VH_B2P-VH_1x02_P3.96mm_Vertical
J40: Conn_01x04; TE_MATE-N-LOK_350211-1_1x04_P5.08mm_Vertical
J41, J42, J43: Conn_01x02; Cinch_Vertical

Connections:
+12L: J30.1, J31.1
+12P: J40.1, J41.2, J42.2, J43.2
+12V: J20.1, J21.1, J22.1, J23.1
+15V: J10.1, J11.1, J12.1
GND: J10.2, J10.MP (MountPin), J11.2, J11.MP (MountPin), J12.2, J20.2, J20.MP (MountPin), J21.2, J21.MP (MountPin), J22.2, J22.MP (MountPin), J23.2, J23.MP (MountPin), J30.2, J30.MP (MountPin), J31.2
unnamed: J40.2, J41.1
unnamed: J40.3, J42.1
unnamed: J40.4, J43.1

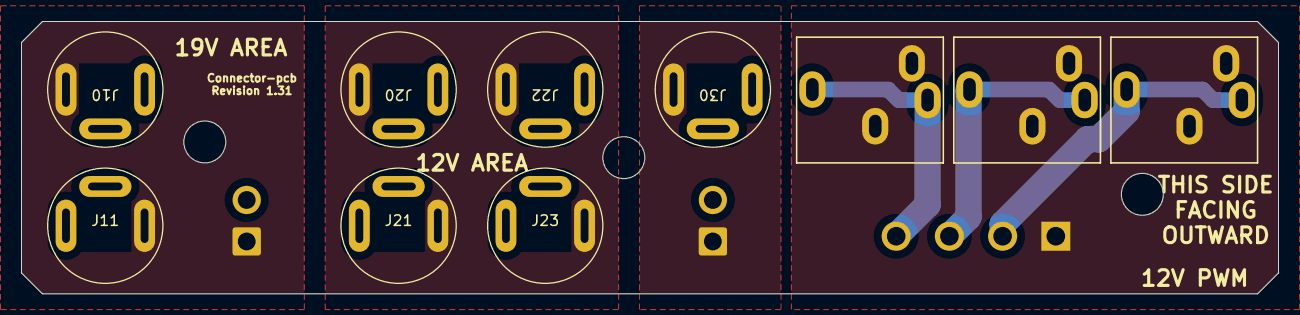
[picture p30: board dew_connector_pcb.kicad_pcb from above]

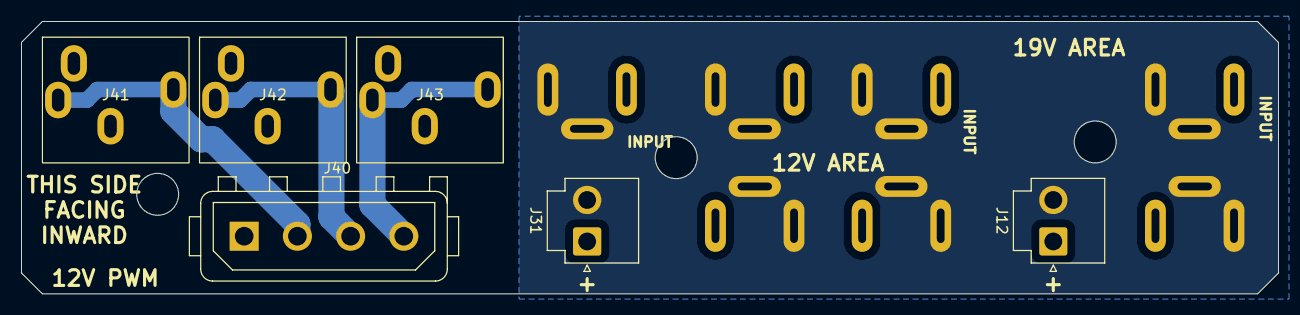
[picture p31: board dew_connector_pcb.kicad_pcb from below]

Board: 2 copper layers, 120.0 x 26.0 mm, 13 parts (6 on the bottom side), 8 nets.

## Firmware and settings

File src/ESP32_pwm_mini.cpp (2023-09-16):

// ======================================================================
// ESP32_pwm_mini DEFINITIONS
// Code for an astronomy dew controller
// (c) Copyright Norman Cleesattel
// DO NOT CHANGE
// ======================================================================

// ======================================================================
// INCLUDES DO NOT CHANGE
// ======================================================================
#include "defines.h"
#include "display.h"
#include "sensor.h"
#include "encoder.h"
#include "pwmchannels.h"
#include "ammeter.h"

// ======================================================================
// DEFINES AND VARIABLES
// ======================================================================
unsigned long currenttime, lowcounter, midcounter, highcounter, ultracounter;

// ======================================================================
// SETUP
// ======================================================================

void setup() {

  // opens serial port, sets data rate to 115200 bps
  Serial.begin(SERIALSPEED);

  // init the display
  init_display();
  init_sensor();
  init_encoder();
  init_pwm();
  init_ammeter();
}

// ======================================================================
// MAIN LOOP
// ======================================================================

void loop() {

  //Serial.print("Code is running on Core: ");Serial.println( xPortGetCoreID());
  static MachineStates machine_state = state_idle;

  currenttime = millis();

  if (currenttime > (ultracounter + ULTRAFREQ)) {
    machine_state = state_ultra;
    ultracounter = currenttime;
  }

  if (currenttime > (highcounter + HIGHFREQ)) {
    machine_state = state_high;
    highcounter = currenttime;
  }

  if (currenttime > (midcounter + MIDFREQ)) {
    machine_state = state_mid;
    midcounter = currenttime;
  }

  if (currenttime > (lowcounter + LOWFREQ)) {
    machine_state = state_low;
    lowcounter = currenttime;
  }

  switch (machine_state) {
    case state_low:
      read_sensor();  // read temperature probes [every second cycle]
      machine_state = state_idle;
      break;

    case state_mid:
      update_display();  // update display [every second cycle]
      update_pwm();      // update pwm [every second cycle]
      machine_state = state_idle;
      break;

    case state_high:
      read_ammeter();  // update amp [every second cycle]
      machine_state = state_idle;
      break;

    case state_ultra:
      read_encoder();  // update encoder [every second cycle]
      machine_state = state_idle;
      break;

    default:
      machine_state = state_idle;
      break;
  }
  //delay(2000);
}

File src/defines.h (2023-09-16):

// ======================================================================
// ESP32_pwm_mini DEFINITIONS
// Code for an astronomy dew controller
// (c) Copyright Norman Cleesattel
// May need to adapt to your hardware
// ======================================================================

#include <Arduino.h>

// ======================================================================
// GLOBAL DEFINES
// ======================================================================
#define SERIALSPEED                 57600

// ======================================================================
// PWM DEFINITIONS
// ======================================================================
const int PWMCHANNELA   = 0;
const int PWMCHANNELB   = 1;
const int PWMFREQ      = 71993;
const int PWMRES       = 8;
const int PWMDUTYCYCLE = 255;
float PWMPOWERA;
float PWMPOWERB;

// ======================================================================
// StateMachine definitions
// ======================================================================
const int LOWFREQ = 3000;   // frequency of main updates in ms
const int MIDFREQ = 400;     // frequency of encoder updates in ms
const int HIGHFREQ = 10;     // frequency of encoder updates in ms
const int ULTRAFREQ = 1;     // frequency of encoder updates in ms
enum MachineStates { state_idle, state_low, state_mid, state_high, state_ultra};
  
// ======================================================================
// HARDWARE MAPPINGS
// ======================================================================

#define SDAPIN                      21                  // SDA
#define SCLPIN                      22                  // SCL

//PWM PINS
const int CH1PWMPIN = 25;  // corresponds to GPIO25
const int CH2PWMPIN = 33;  // corresponds to GPIO33
const int CH3PWMPIN = 32;  // corresponds to GPIO32

//CURRENT MEASUREMENT
const int CH1AMPPIN = 26;  // corresponds to GPIO26
const int CH2AMPPIN = 27;  // corresponds to GPIO27
const int CH3AMPPIN = 14;  // corresponds to GPIO14

//VOLTAGE MEASUREMENT
const int VOLTPIN = 13;  // corresponds to GPIO13

//TEMPERATURE MEASUREMENTS
const int CH1TEMPPIN = 19;  // corresponds to GPIO19
const int CH2TEMPPIN = 18;  // corresponds to GPIO18

//ROTARY ENCODER INPUTS
const int RB_CLK = 39;  // corresponds to GPIO39
const int RB_DT  = 36;  // corresponds to GPIO36
const int RB_SW  = 16;  // corresponds to GPIO16

const int RA_CLK = 34;  // corresponds to GPIO35
const int RA_DT  = 35;  // corresponds to GPIO34
const int RA_SW  = 17;  // corresponds to GPIO17

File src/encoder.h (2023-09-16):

// ======================================================================
// ESP32_pwm_mini DEFINITIONS
// Code for an astronomy dew controller
// (c) Copyright Norman Cleesattel
// DO NOT CHANGE
// ======================================================================

// ======================================================================
// INCLUDES DO NOT CHANGE
// ======================================================================


// ======================================================================
// DEFINES AND VARIABLES
// ======================================================================
int lim_volt = 500;             // voltage threshold be interpreted as 1
int counterA = 50;
int counterB = 50;

int currentStateCLKA;
int currentStateCLKB;
static int lastStateCLKA;
static int lastStateCLKB;

int currentStateCLK_aA;
int currentStateCLK_aB;
static int lastStateCLK_aA;
static int lastStateCLK_aB;

int currentStateDT_aA;
int currentStateDT_aB;
int currentStateDTA;
int currentStateDTB;

String currentDirA = "";
String currentDirB = "";
unsigned long lastButtonPressA = 0;
unsigned long lastButtonPressB = 0;

int count = 0;


// ======================================================================
// SETUP
// ======================================================================
void init_encoder() {
  // Set encoder pins as inputs
  pinMode(RA_CLK, INPUT);
  pinMode(RA_DT, INPUT);
  pinMode(RA_SW, INPUT_PULLUP);

  pinMode(RB_CLK, INPUT);
  pinMode(RB_DT, INPUT);
  pinMode(RB_SW, INPUT_PULLUP);

  // Read the initial state of CLK
  lastStateCLK_aA = analogRead(RA_CLK);
  if (lastStateCLK_aA < lim_volt) {
    lastStateCLKA = 0;
  } else {
    lastStateCLKA = 1;
  }

  // Read the initial state of CLK
  lastStateCLK_aB = analogRead(RB_CLK);
  if (lastStateCLK_aB < lim_volt) {
    lastStateCLKB = 0;
  } else {
    lastStateCLKB = 1;
  }
  delay(1000);
}

// ======================================================================
// CODE
// ======================================================================
void read_encoder() {


  // Read the current state of CLK
  currentStateCLK_aA = analogRead(RA_CLK);
  if (currentStateCLK_aA < lim_volt) {
    currentStateCLKA = 0;
  } else {
    currentStateCLKA = 1;
  }

  currentStateDT_aA = analogRead(RA_DT);
  if (currentStateDT_aA < lim_volt) {
    currentStateDTA = 0;
  } else {
    currentStateDTA = 1;
  }

  // If last and current state of CLK are different, then pulse occurred
  // React to only 1 state change to avoid double count
  if (currentStateCLKA != lastStateCLKA && currentStateCLKA == 1) {

    // If the DT state is different than the CLK state then
    // the encoder is rotating CCW so decrement
    if (currentStateDTA != currentStateCLKA) {
      if (counterA > 0) {
        counterA -= 10;
      }
      currentDirA = "CCW";
    } else {
      // Encoder is rotating CW so increment
      if (counterA < 100) {
        counterA += 10;
      }
      currentDirA = "CW";
    }

    //Serial.print("Direction: ");
    //Serial.print(currentDirA);
    //Serial.print(" | Counter: ");
    //Serial.println(counterA);
  }

  // Remember last CLK state
  lastStateCLKA = currentStateCLKA;

  // Read the current state of CLK
  currentStateCLK_aB = analogRead(RB_CLK);
  if (currentStateCLK_aB < lim_volt) {
    currentStateCLKB = 0;
  } else {
    currentStateCLKB = 1;
  }

  currentStateDT_aB = analogRead(RB_DT);
  if (currentStateDT_aB < lim_volt) {
    currentStateDTB = 0;
  } else {
    currentStateDTB = 1;
  }

  // If last and current state of CLK are different, then pulse occurred
  // React to only 1 state change to avoid double count
  if (currentStateCLKB != lastStateCLKB && currentStateCLKB == 1) {

    // If the DT state is different than the CLK state then
    // the encoder is rotating CCW so decrement
    if (currentStateDTB != currentStateCLKB) {
      if (counterB > 0) {
        counterB -= 10;
      }
      currentDirB = "CCW";
    } else {
      // Encoder is rotating CW so increment
      if (counterB < 100) {
        counterB += 10;
      }
      currentDirB = "CW";
    }

    //Serial.print("Direction: ");
    //Serial.print(currentDirB);
    //Serial.print(" | Counter: ");
    //Serial.println(counterB);
  }

  // Remember last CLK state
  lastStateCLKB = currentStateCLKB;


  //delay(1);
}

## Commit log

2023-09-24 Add pictures
    [CONNECTOR_PRINT.stl, DISPLAY_PRINT.stl, KNOB_SOCKET.stl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]
2023-09-24 Add dew connector pcb
    [BOM-dew_connector_pcb.csv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]
2023-09-24 Add dew control pcb
    [BOM-dew_control_pcb.csv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]
2023-09-24 Add dew sensor pcb
    [BOM-dew_sensor_pcb.csv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]
